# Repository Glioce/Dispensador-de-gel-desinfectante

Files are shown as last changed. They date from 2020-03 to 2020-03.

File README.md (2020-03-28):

# Dispensador de Gel Desinfectante
*Convierte un producto de higiene en algo más higiénico*
*#CienciaEnCasa*

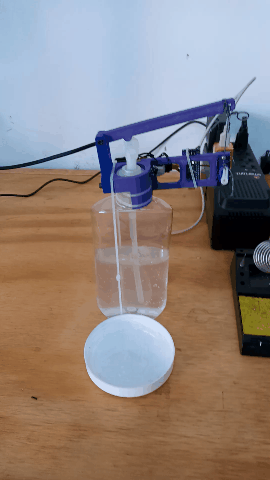
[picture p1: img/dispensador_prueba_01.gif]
Gif mostrando el funcionamiento del dispensador


Lavarse las manos regularmente en una buena forma de evitar enfermedades. 
Con ello evitamos la propagación de gérmes y que esos gérmenes entren a nuestro cuerpo. 
En lugares en los que no tenemos agua y jabón disponible, el gel desinfectante es una 
buena opción para mantener nuestras manos libres de gérmenes.

En este artículo se explican los pasos para armar un dispensador automático de gel 
desinfectante. Se instala sobre un dispensador común y permite extraer gel sin 
necesidad de tocarlo.

## Paso 1: Reunir los materiales
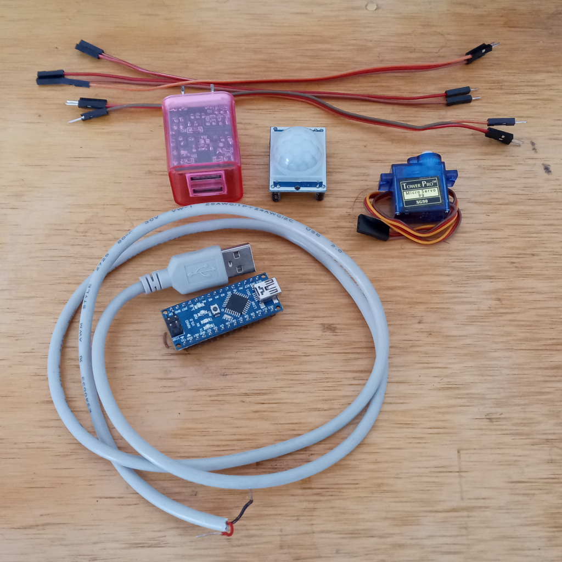
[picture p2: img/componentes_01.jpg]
Foto de componentes

+ 1 Sensor Reflectivo TCRT5000
+ 1	Resistencia 100 ohm
+ 1	Resistencia 10 kohm
+ 1	Arduino Nano
+ 1	Servo SG90
+ 1	Cable para Fuente USB
+ 1	Fuente Cargador USB 5V
+ 8	Jumpers
+ 3	Pines macho
+ 3	Cinchillos de plástico
+ 2	Tornillos M3 x 10
+ 2 Tornillos M3 x 20
+ 1 Tornillo M3 x 25
+ 1 Tuerca M3
+ Impresión 3D

### Paso 1.1: Impresión 3D
Las piezas se imprimieron en **PLA** usando los siguientes parámetros:  
Slicer: Ultimaker Cura  
Impresora: Ender 3  
Calidad: Baja (altura de capa 0.28 mm)  
Infill: 20 %  
No requieren soportes y se pueden imprimir juntas o separadas.  
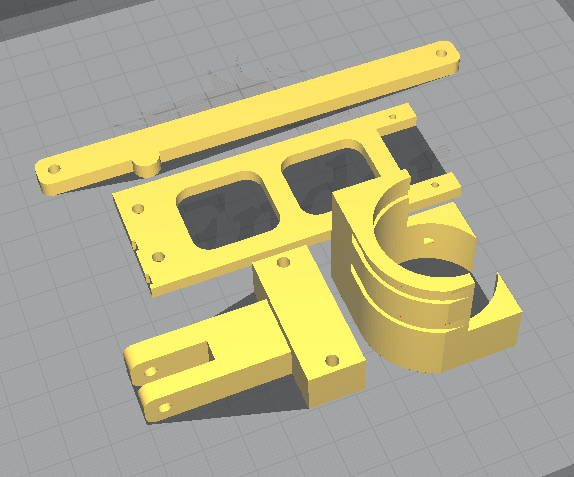
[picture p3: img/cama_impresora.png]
Captura de Cura


## Paso 2: Armar circuito
Esquemático
El circuito tiene 4 componentes principales: la fuente de alimentación; un sensor infrarrojo que detecta si hay un objeto cercano; un Arduino que lee el estado del sensor y envía pulsos al servo; y el servo que mueve la palanca del dispensador. 

### Paso 2.1: Sensor infrarrojo
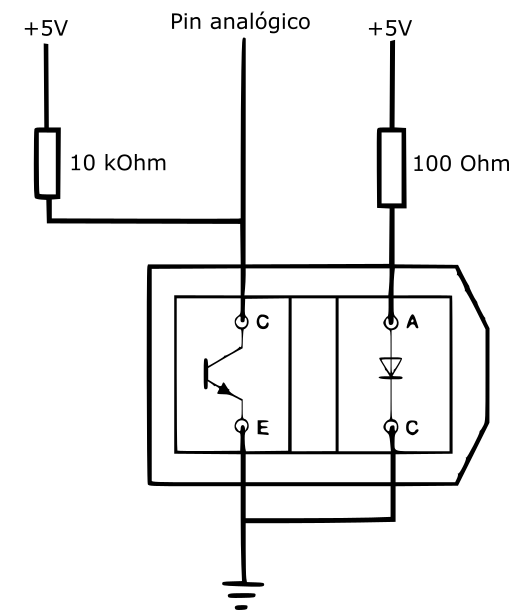
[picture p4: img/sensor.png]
Esquemático del sensor

El sensor está formado por un TCRT5000 y dos resistencias.  
Cortar el pin positivo del diodo infrarrojo. Soldar resistencias y tres pines para formar el circuito que se muestra arriba. Así es más fácil conectar con jumpers.

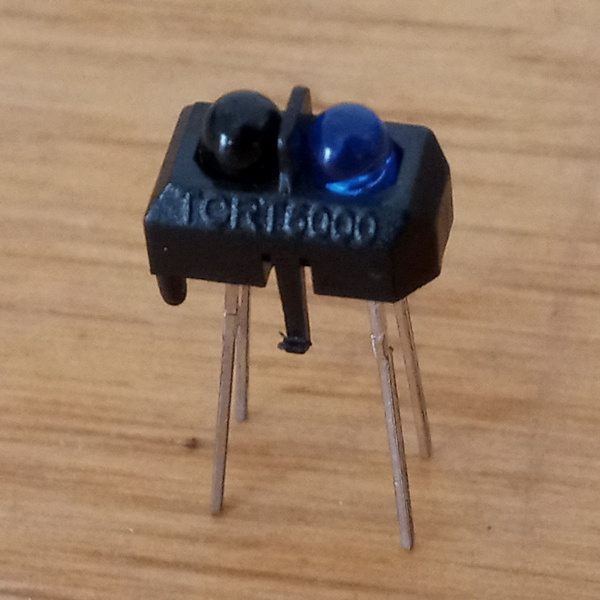
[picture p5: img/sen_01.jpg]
TCRT5000 original

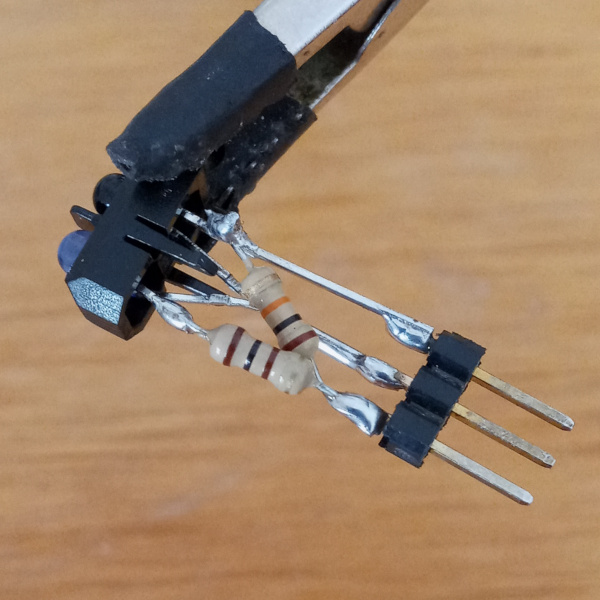
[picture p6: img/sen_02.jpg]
TCRT5000 con resistencias y pines

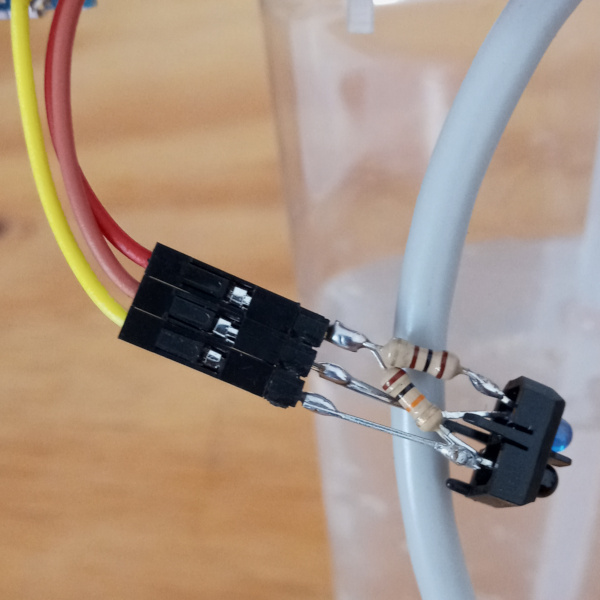
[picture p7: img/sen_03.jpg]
TCRT5000 conectado con jumpers


### Paso 2.2: Cables de alimentación
Usamos 2 jumpers hembra para alimentar el Arduino a través de las terminales GND y 5V.
Otros 3 jumpers hembra se usan para conectar el sensor (GND-café, 5V-rojo, Salida-amarillo).
El servo se conecta con 3 jumpers macho (café, rojo y naranja).

Cortar los 3 jumpers rojos y los 3 jumpers cafés, pelar las puntas y unir los cables.
También unir las puntas del cable USB y aplicar soldadura. Aislar con tubo termoretráctil (thermofit).

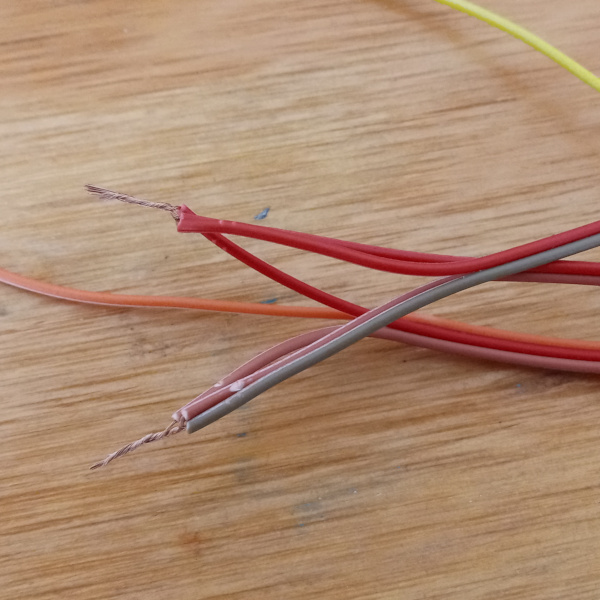
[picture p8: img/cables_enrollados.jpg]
Cables enrollados

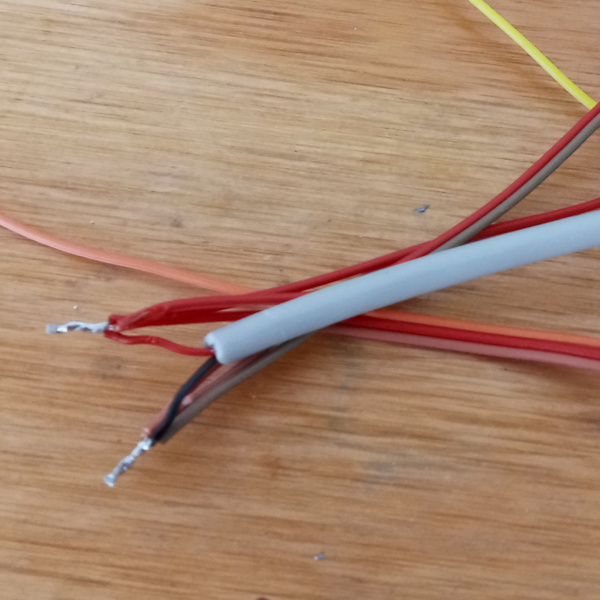
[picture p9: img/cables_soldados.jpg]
Cables soldados

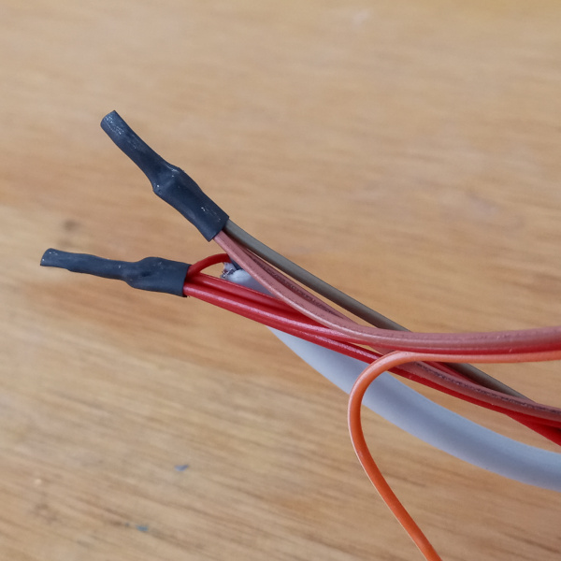
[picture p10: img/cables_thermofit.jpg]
Cables con thermofit


### Paso 3.3: Conexiones finales
Conectar jumpers al servo. Conectar jumpers al Arduino.

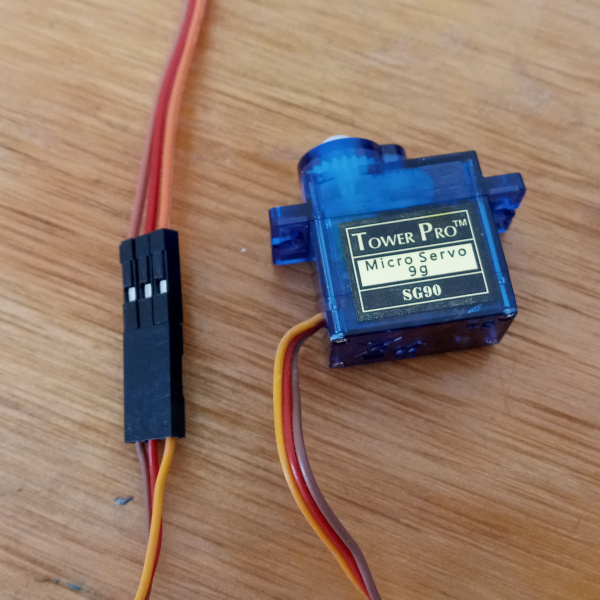
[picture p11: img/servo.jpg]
servo

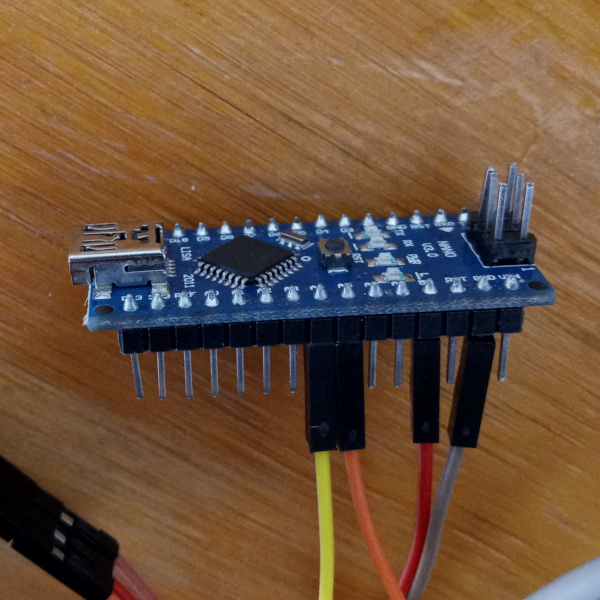
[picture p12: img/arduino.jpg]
Arduino


## Paso 4: Unir piezas de impresión 3D
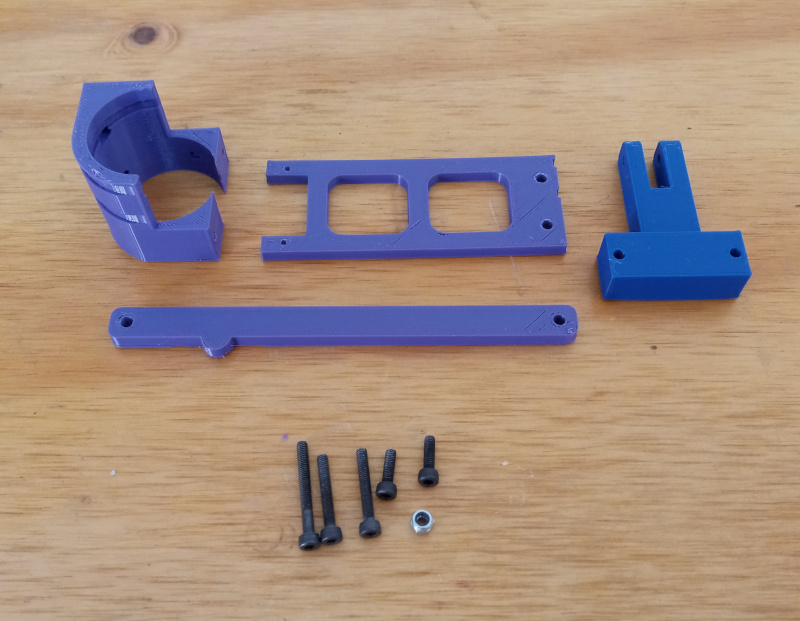
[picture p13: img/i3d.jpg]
todas las piezas
  

Coloca 2 tornillos M3x10 en la pieza que parece una escalera, después atornilla en la pieza cilíndrica.
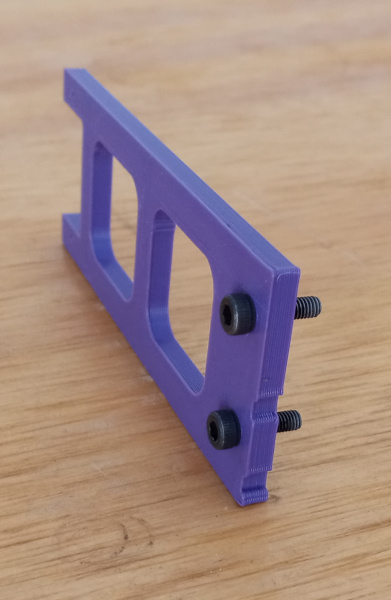
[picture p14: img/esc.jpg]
escalera

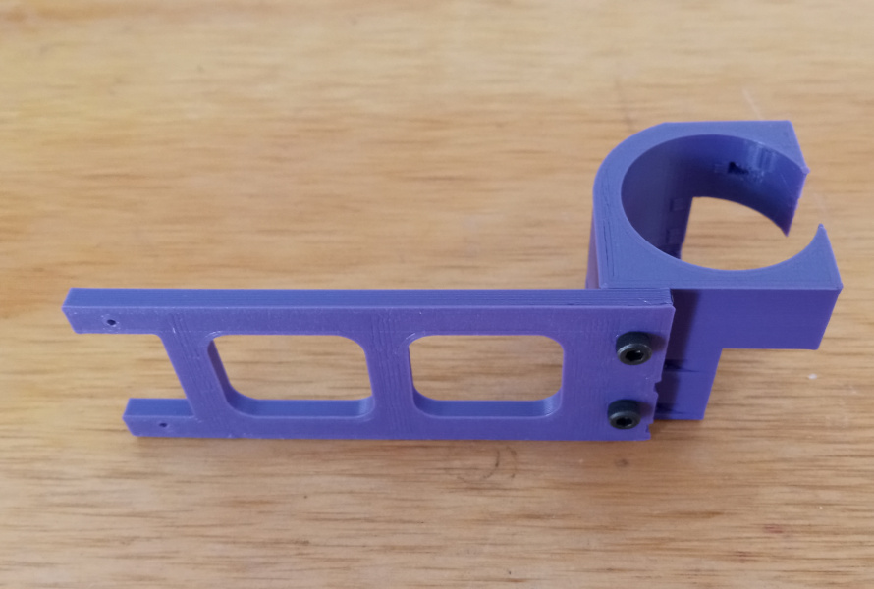
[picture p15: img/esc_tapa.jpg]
escalera atornillada


Coloca el esamblaje anterior en la tapa del dispensador. Luego inserta dos tornillos M3x20 en la pieza con una ranura. También se atornilla en la pieza cilíndrica.
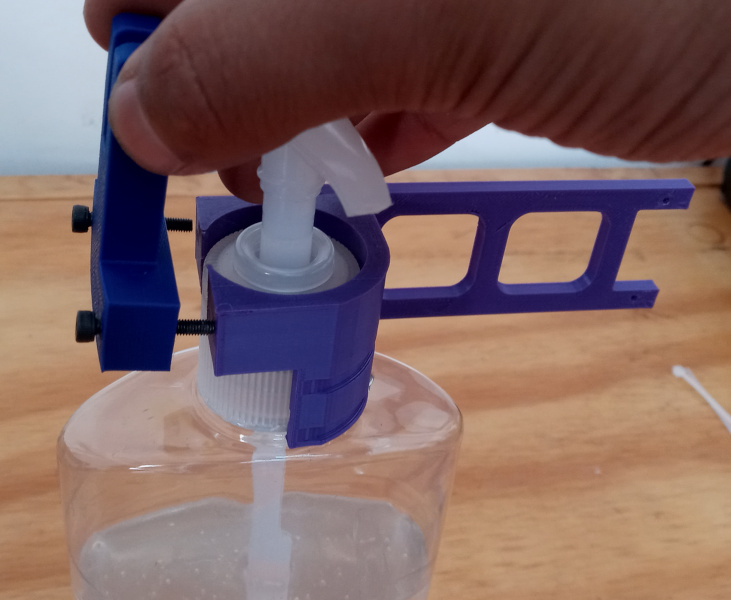
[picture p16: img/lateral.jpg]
pieza con ranura y tornillos


Inserta la palanca en la pieza con ranura. Usa un tornillo M3x25 y una tuerca para unir las piezas sin apretar demasiado para que la palanca pueda rotar libremente.  
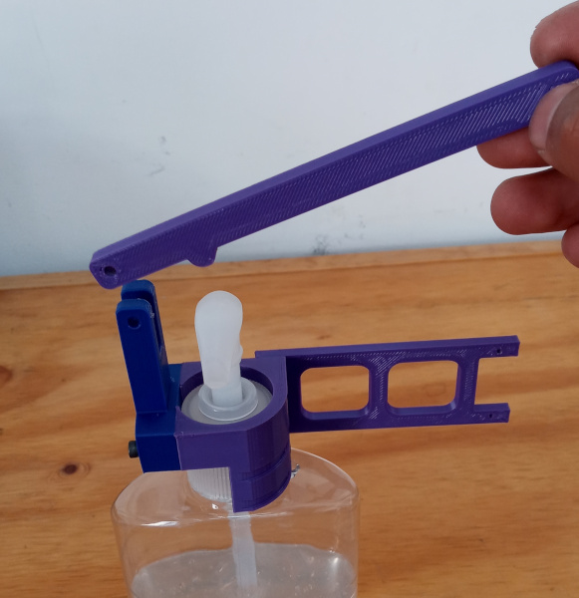
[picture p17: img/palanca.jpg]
palanca


Fijar todo el ensamblaje a la tapa con cinchillos de plástico
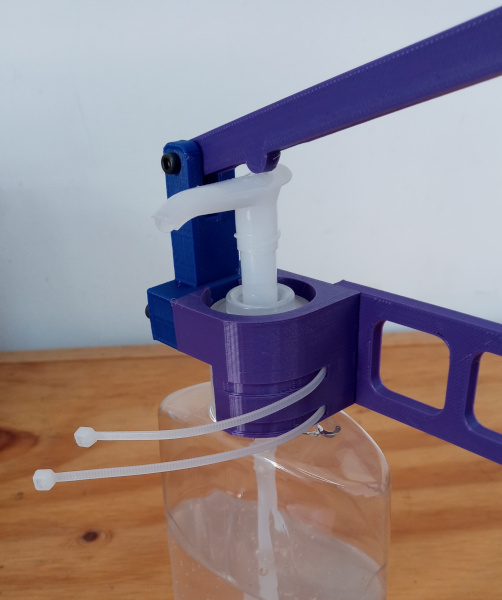
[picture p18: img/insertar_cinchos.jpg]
insertar cinchos

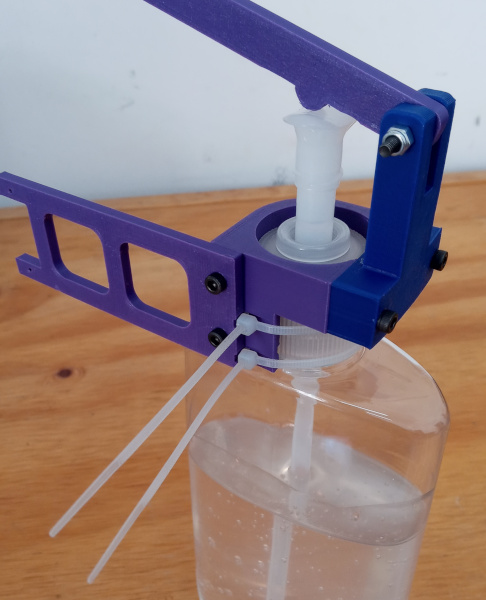
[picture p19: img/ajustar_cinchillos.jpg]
ajustar cinchillos


## Paso 5: Instalar componentes electrónicos
Atornillar el servomotor en el extremo de la pieza que parece escalera
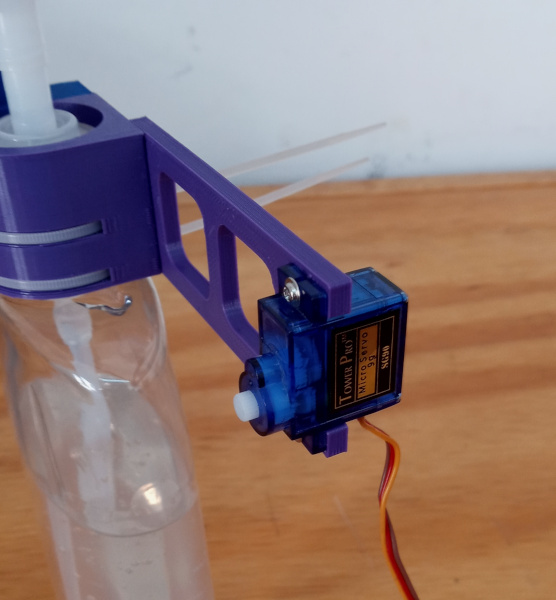
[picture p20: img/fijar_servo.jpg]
fijar servo


Fijar el Arduino, el sensor y los cables a la pieza que parece escalera con cinchillos y alambre
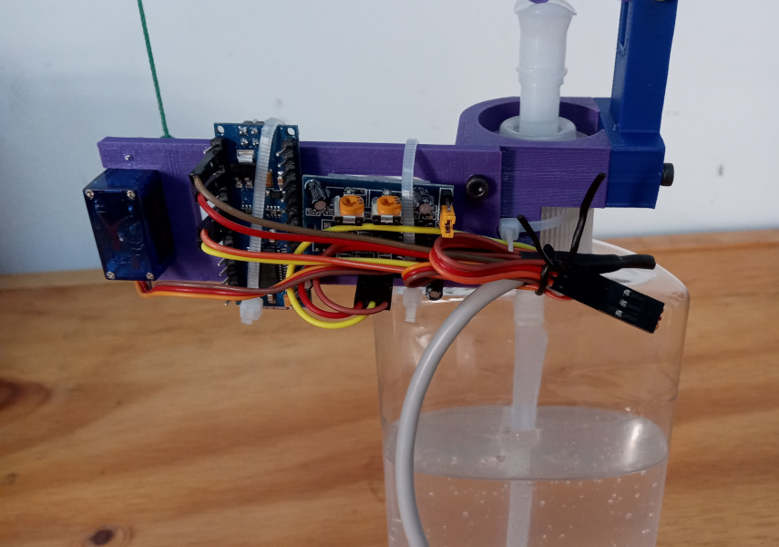
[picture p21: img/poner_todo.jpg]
fijar cables


## Paso 6: Ajustes
Si no has programado el Arduino, ahora es el momento, descarga el código del repositorio y ...
Es recomendable desconectar los cables del servomotor para que no se mueva mientras se realiza la programación.

Conecta el cargador USB a la toma de corriente y el cable de alimentación al cargador para encender el circuito.
El servo se moverá a la posición inical, donde la palanca se encuentra levantada. Ahora desconecta el circuito.
Instala el accesorio del servo, debe quedar apuntando hacia arriba. Amarra un hilo en la punta del accesorio.
Después inserta el hilo en el orificio de la palanca y jala hacia abajo para tensarlo, 
de modo que presione un poco la bomba del dispensador. Amarra el hilo sin que deje de estar tenso.

Ya está listo.

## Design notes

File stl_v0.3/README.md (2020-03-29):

Archivos STL para impresión 3D

Se pueden imprimir en capas de 0.3 mm, sin soportes

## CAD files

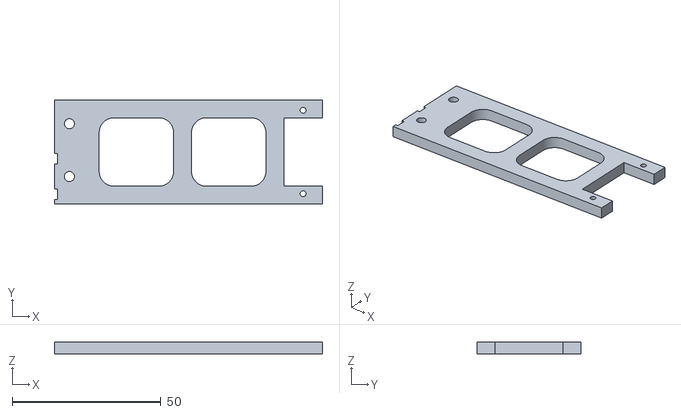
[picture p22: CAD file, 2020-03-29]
stl_v0.3/escalera.stl
90.0 x 35.0 x 4.00

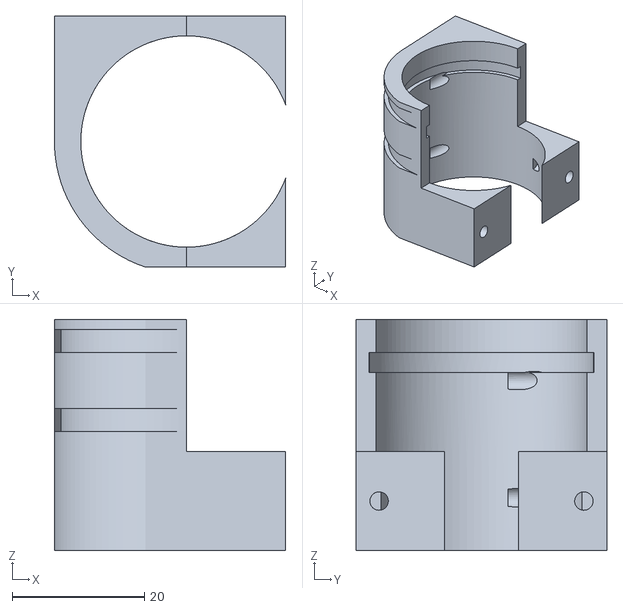
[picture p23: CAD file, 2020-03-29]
stl_v0.3/cilindrico.stl
35.0 x 38.0 x 35.0

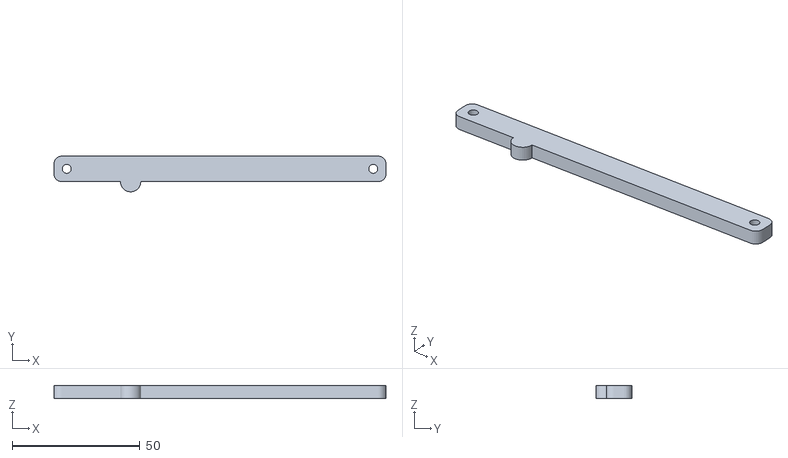
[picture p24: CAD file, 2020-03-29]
stl_v0.3/palanca.stl
130.0 x 14.0 x 5.00

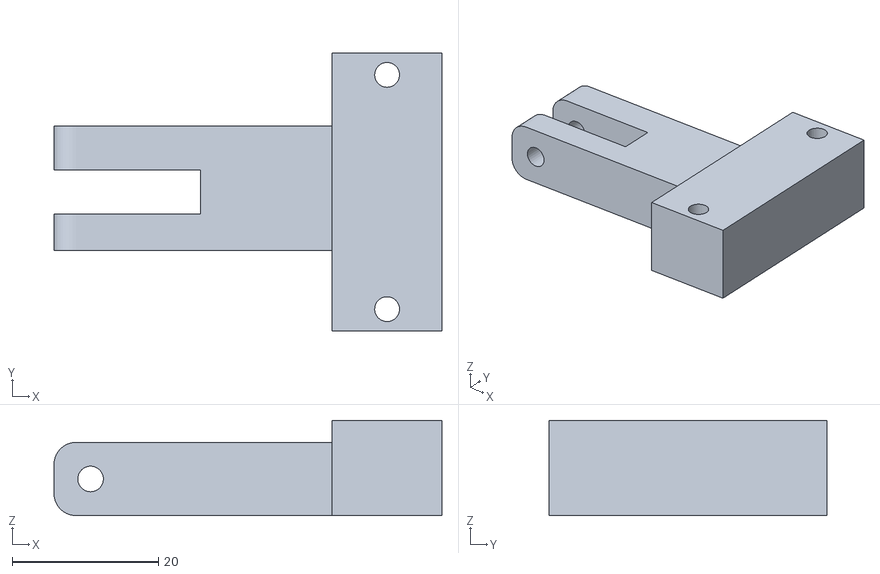
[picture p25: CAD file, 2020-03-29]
stl_v0.3/ranura.stl
53.0 x 38.0 x 13.0

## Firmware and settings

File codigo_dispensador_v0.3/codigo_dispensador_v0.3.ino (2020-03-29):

/* DESPACHADOR DE GEL ANTIBACTERIAL PARA MANOS V0.3
 * 
 * Un servomotor mueve una palanca que presiona una bomba de
 * gel antibacterial. El servo es controlado por un Arduino Nano 
 * y un sensor. En esta versión se usa un sensor infrarrojo TCRT5000.
 */
 
#define PIN_SENSOR A4
#define PIN_SERVO A5
#define PIN_LED 13

#include <Servo.h>
Servo servo;

int sen = 0; //estado actual del sensor

// Umbral de detección (valores de 0 a 1024)
// Si el valor es grande incrementa la sensibilidad
// Si el valor es pequeño disminuye la sensibilidad
#define UMBRAL 600

void setup() {
  pinMode(PIN_SENSOR, INPUT);
  sen = analogRead(PIN_SENSOR); //primera lectura
  
  pinMode(PIN_LED, OUTPUT);
  digitalWrite(PIN_LED, 0); //LED apagado
  
  servo.attach(PIN_SERVO);
  servo.write(180); //levantar palanca
}

void loop() {
  sen = analogRead(PIN_SENSOR);
  
  if (sen < UMBRAL) {
    servo.write(0); //bajar palanca
    digitalWrite(PIN_LED, 1); //LED indica que el sensor detecta un objeto
  }
  else {
    servo.write(180); //levantar palanca
    digitalWrite(PIN_LED, 0); //LED indica que el sensor no detecta un objeto
  }
  
  delay(20); //tiempo de espera entre loops
}

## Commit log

2020-03-27 cambiar nombre de 2 imgs
2020-03-28 imgs del sensor
2020-03-28 otra img del sensor
2020-03-28 foto que faltaba
2020-03-29 subir stls y cambiar nombre de codigo
    [cilindrico.stl, escalera.stl, palanca.stl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]
2020-03-29 cambiar orientación
    [cilindrico.stl, escalera.stl, palanca.stl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]
